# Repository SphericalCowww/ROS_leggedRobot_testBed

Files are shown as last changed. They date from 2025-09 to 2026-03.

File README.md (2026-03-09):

# Testing for Legged Robot using ROS2

Goal: quadruped robot dog with 12 DOF up to a simple walk gait.

Derivation from the following <a href="https://github.com/SphericalCowww/ROS_init_practice">GitHub Repository</a>.

The CAD drawings are "hidden" under this  <a href="https://github.com/SphericalCowww/ROS_leggedRobot_testBed/tree/main/src/my_robot_description/mesh/CADv0.1">path</a> for ROS reason.

## Hardware Connections

| device | DYNAMIXEL models | number | specification |
| - | - | - | - |
| controller | <a href="https://www.raspberrypi.com/products/raspberry-pi-5/">rasp pi 5</a> | 1 | 16Gb RAM | 
| DC-DC step-down convertor | Hailege <a href="https://www.amazon.de/Hailege-Module-Step-Down-Supply-Converter/dp/B07XFMMY1F">24V/12V to 5V/5A</a> | 1 | USB Port port to rasp pi 5,  DC 5.5mm x 2.5mm Male to battery | 
| USB communication interface | DYNAMIXEL <a href="https://emanual.robotis.com/docs/en/parts/interface/u2d2/">U2D2</a> | 1 | Can control 12 servo in daisy chain if properly powered |
| communication/power hub | DYNAMIXEL <a href="https://emanual.robotis.com/docs/en/parts/interface/u2d2_power_hub/">U2D2 power hub board</a> | 2 | Operating voltage	3.5-24V withg a maximum current	of 10A |
| servo motor | DYNAMIXEL <a href="https://emanual.robotis.com/docs/en/dxl/x/xl430-w250/">XL430-W250-T</a> | 12 | Max stall torque: 1.5 N*m (at 12.0V, 1.4A, 1.071 Nm/A) |
| battery | ZYGY <a href="https://www.amazon.de/dp/B0BB6RMM5Q">11.1V 2000mAh</a> | 2 | already includes protection. Need adapters for: T-plug => XT60 Male => DC 5.5mm x 2.5mm Male | 
| bearings | standard bearing, threaded rod, rod-end bearing, <a href="https://www.amazon.de/dp/B01M2ZCLKX">spacer</a> | 8, 4, 4, 4 | as long as the dimensions work out together, but the rod length so far is 60mm |
| bolts and nuts | | | DYNAMIXEL provides most < M3 bolts; use lock nuts; also best to have threaded inserts for 3D-printer materials, but designed choices can get around it |
|  |  |  |  | 
| battery | Palogreen <a href="https://www.amazon.de/dp/B0DZ65LMPT">12.6V DC Akku 2800mAh</a> | - | already includes protection. One for powering the rasp pi 5, and several backups | 
| power supply | SMPS | - | 12V/5A to test 1 leg | 
| battery | <a href="https://secure.reichelt.com/de/en/industrial_cell_18650_3_6_v_2600_mah_unprotected_pack_of_2-p261054.html">SON 18650 VTC5A</a> | - | Operating voltage 3.6-3.7V with a discharge max of 10A each; need 3 parallel of 3 in series | 
| battery management system | <a href="https://powercells.de/3s-40a-12-6v-cell-li-on-akku-batterie-schutz-platine-bms-pcb-lithium-protection.html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">3S 40A 12.6V BSM PCB</a> | - | plan to use one for each of the 3-series battery pack | 
| controller | <a href="https://emanual.robotis.com/docs/en/parts/controller/opencr10/">OpenCR 1.0</a> | - | This is not necessary if a Rasp Pi is already in use |

#### XL430-W250-T dimensions

  * general dimension: 28.5 x 46.5 x 34 [WxHxD mm]
  * screw size: M2 on rotor plate, M2.5 screws on frame corners, M2.6 on frame surfaces
  * <a href="https://en.robotis.com/service/downloadpage.php?ca_id=70">CAD download</a>
  * bracket reference: <a href="https://grabcad.com/library/openmanipulator-x-frame-set-rm-x52-1">OpenManipulator-X</a>

#### 3D CAD dimensions

  * using 3M screws overall, as they are much more common. Piece thickness will be 4mm, except when a 3M screw is required on the thickness axis, then it's 6mm. For aperture dimension, 1.7mm radius for clearance, and 1.25mm for tapped without a heated insert.

### Power System

  * The daisy chain is recommended to chain 4 or fewer servos to avoid delay
  * Plan to use 2 U2D2 power hub boards controlled by one U2D2. Each hub can be powered independently and controlled by a single U2D2 as long as they share the TTL connection. This requires a Y-cable from U2D2 to the 2 hubs; may need to custom-connect two <a href="https://emanual.robotis.com/docs/en/dxl/x/xl320/#connector-information">MOLEX 51065-0300</a> cables to make a Y-cable.
  * Plan to power the hubs using their SMPS DC jacks. Then use the molex/screw terminal as an output to power the Raspberry Pi 5 via a 12V-to-5V DC-DC converter.

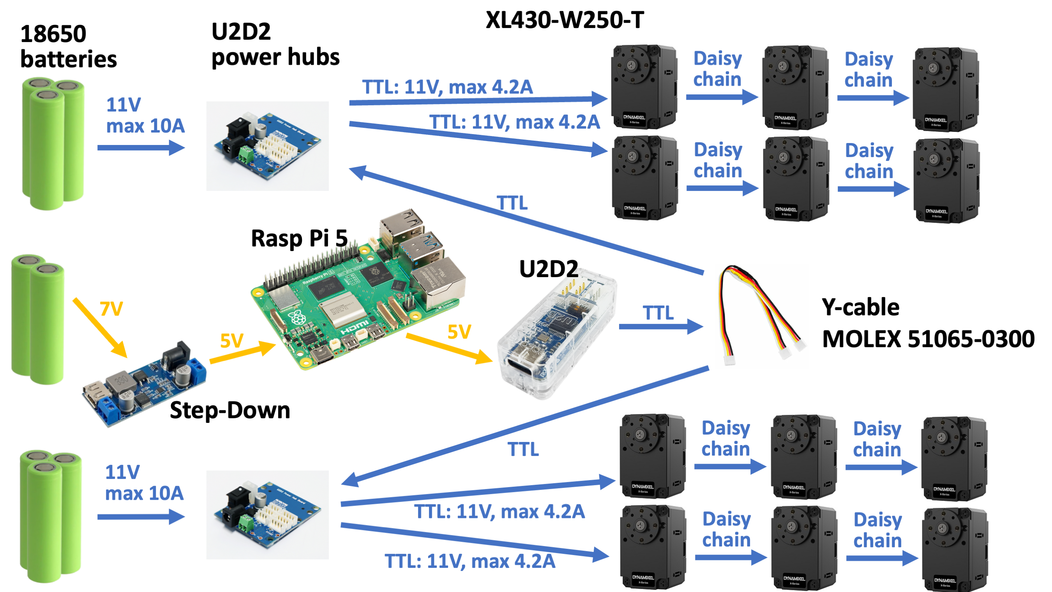
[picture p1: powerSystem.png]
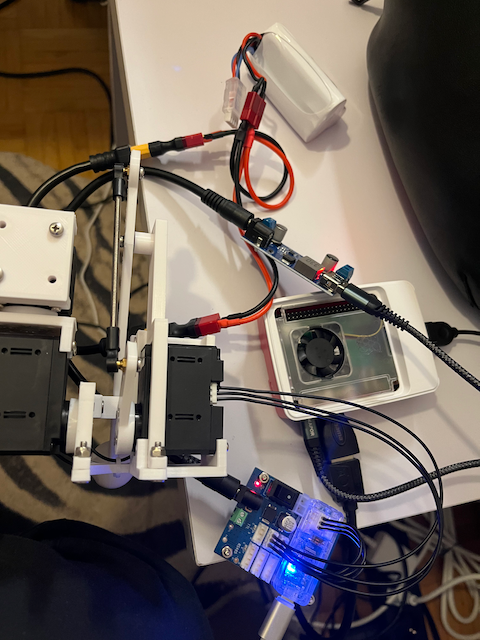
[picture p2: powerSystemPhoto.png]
 

When testing, the 11.1V battery can be teed to power both rasp pi and 3 servos. However, rasp pi does show low power when also turning on the monitor with HDMI connection.

### setting the servo IDs

Connecting servo to U2D2 according to <a href="https://www.youtube.com/watch?v=FIj_NULYOKQ">YouTube</a>:

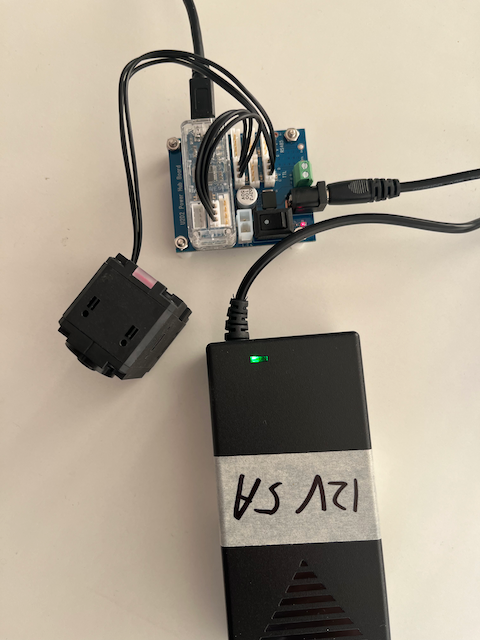
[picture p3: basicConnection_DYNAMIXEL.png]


Use the following App <a href="https://emanual.robotis.com/docs/en/software/dynamixel/dynamixel_wizard2/">DYNAMIXEL Wizard 2.0</a> to change the servo ID (default 1) to, say, ID 10. Note that if any of the servos have the same ID, they will NOT show up in the scan. The servos also all initially come with an ID of 1, so they must be connected one by one to U2D2 to change their IDs accordingly.

    connect U2D2 to computer => open DYNAMIXEL Wizard 2.0
    # Options 
    ## Select protocol to scan => Protocol 2.0 (only)
    ## Select port to scan => which ever port is connected
    ## Select baudrate to scan => 57600 bps and 2000000bpt => OK
    ## Select ID range to scan => End => 50
    ## OK
    # Scan
    # Item 
    ## (Address 7) ID => ID 11 (on the right) => Save (may need to scroll down) 
    ## (Address 8) Baud Rate (Bus) => 2Mbps (on the right) => Save (may need to scroll down) 
    ## (Address 9) Return Delay Time => 0 (on the right) => Save (may need to scroll down) 
    ## (Address 68) Status Return Level => 2 (on the right) => Save (may need to scroll down) 

Can also test out the servo:

    # LED (top right toggle)
    # Torque (top right toggle) => set the value for motion (can select Velocity/Position mode)

### Quadruped: CAD Model and Physical Assembly

One leg assembly needs 3 servos to ensure all 3 degrees of freedom for each of the 4 leg tips:

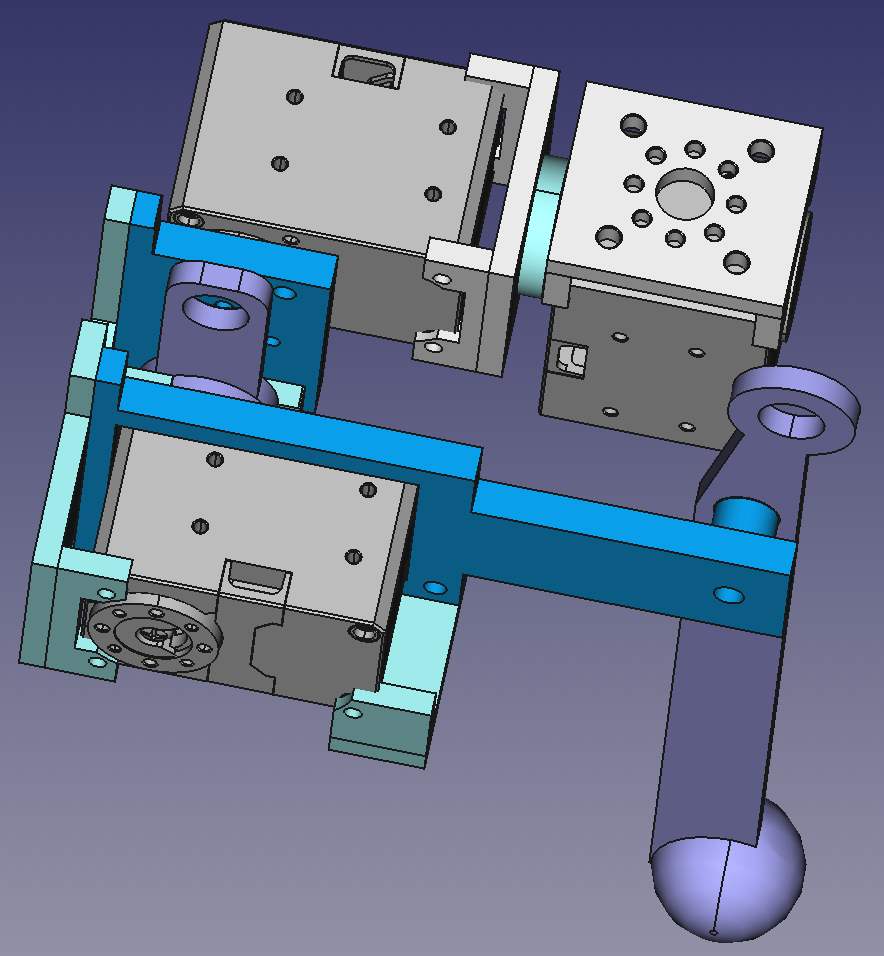
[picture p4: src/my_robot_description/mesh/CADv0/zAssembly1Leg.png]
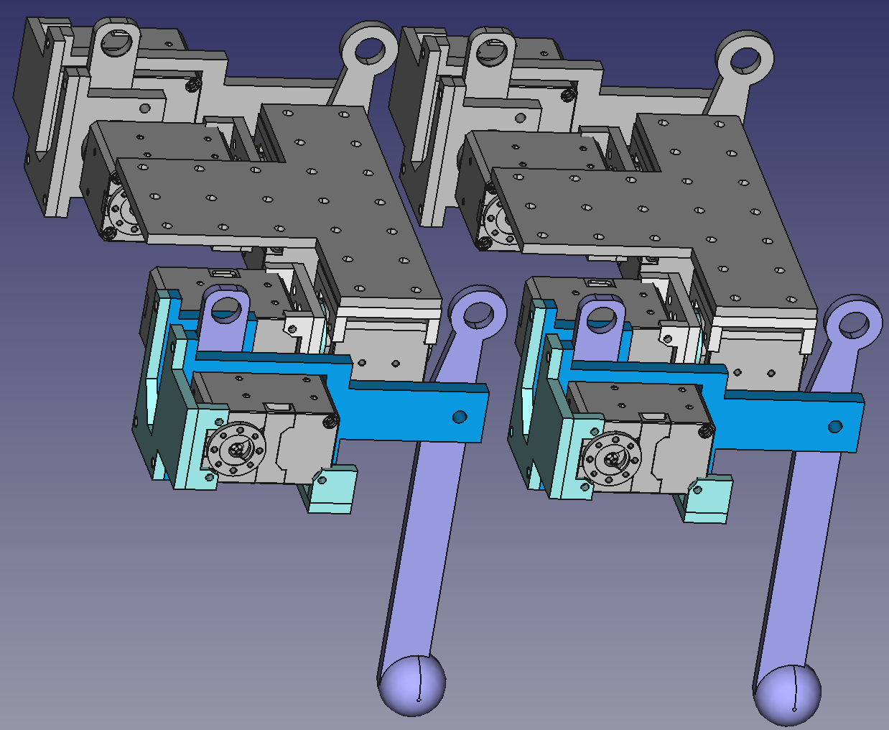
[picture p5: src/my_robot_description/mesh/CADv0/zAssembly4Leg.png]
 

The current design has many flaws, but here is the first assembly:

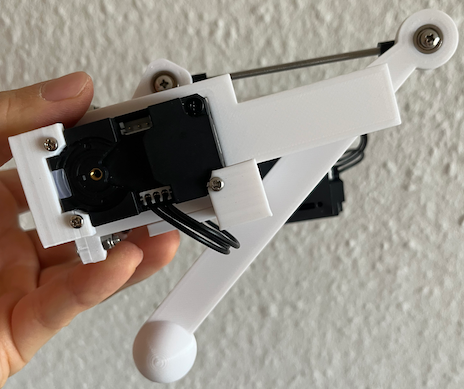
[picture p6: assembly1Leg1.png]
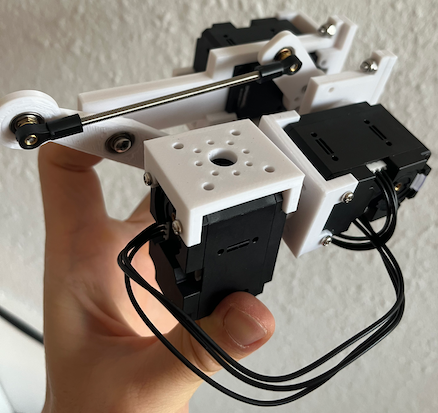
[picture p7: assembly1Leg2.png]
 

[Video demo1](https://raw.githubusercontent.com/SphericalCowww/ROS_leggedRobot_testBed/main/assembly1Leg1.mp4), [video demo2](https://raw.githubusercontent.com/SphericalCowww/ROS_leggedRobot_testBed/main/assembly1Leg2.mp4)

Here is the assembly with the hardware control system: rasp pi 5, DC-DC step-down convertor, U2D2, battery pack, and the existing 1 leg. DO NOT wrap the USB signal cable with the power cables; it would create interference.

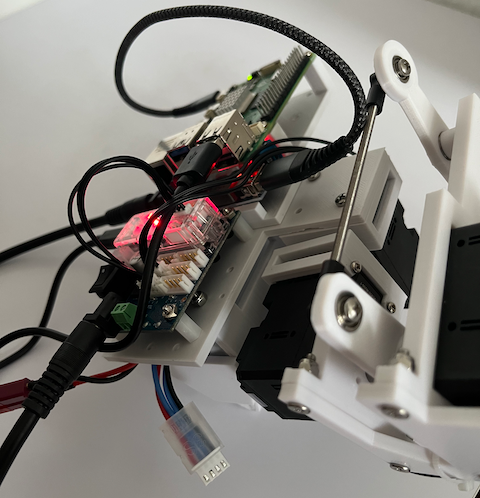
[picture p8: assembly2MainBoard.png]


Here is the full assembly. Also updated the unnecessary bearing at the connection of the universal bearings. The robot has a total weight of roughly 2kg.

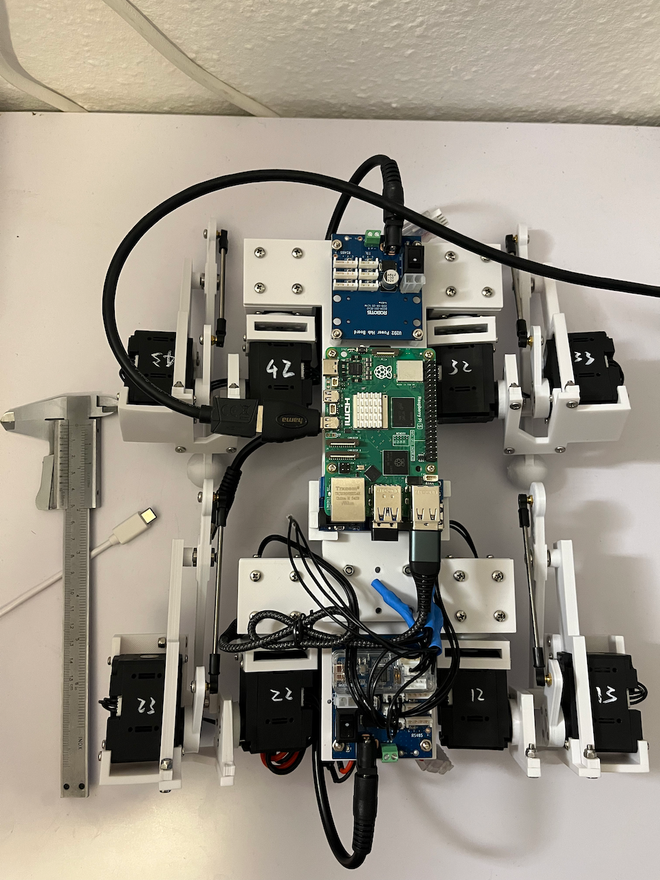
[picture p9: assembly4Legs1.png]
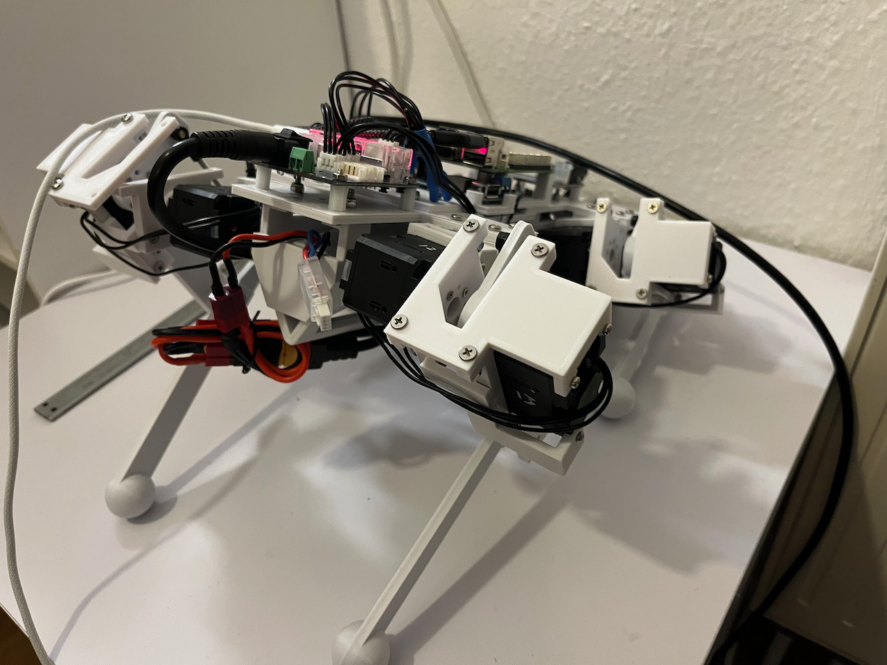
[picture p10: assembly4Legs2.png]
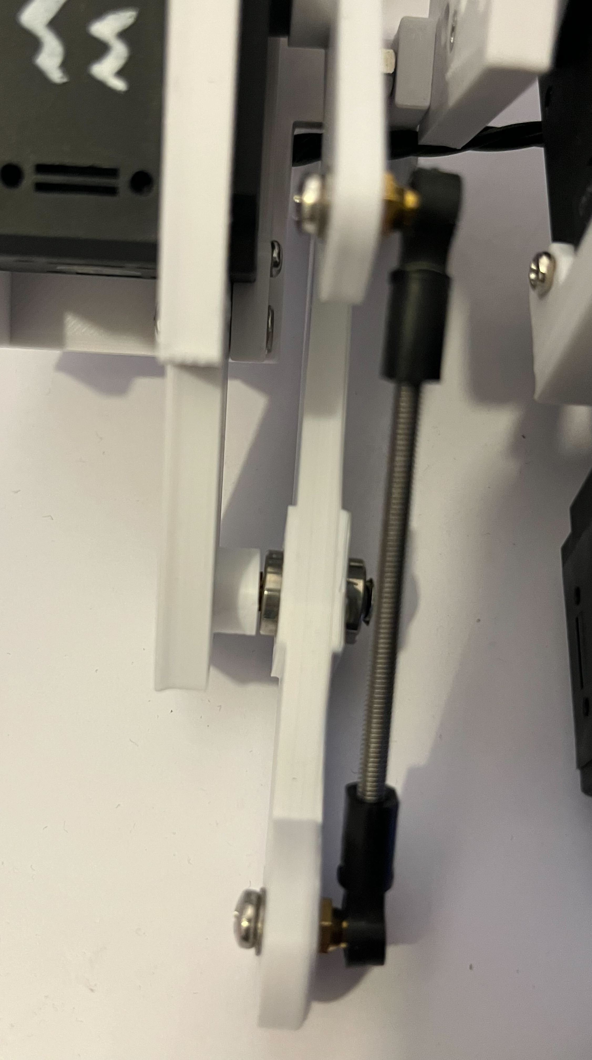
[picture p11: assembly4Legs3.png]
  

## Installing the <a href="https://github.com/ROBOTIS-GIT/DynamixelSDK">dynamixel-sdk</a> and  <a href="https://github.com/ROBOTIS-GIT/dynamixel-workbench">dynamixel-workbench</a>

Following <a href="https://github.com/SphericalCowww/ROS_init_practice">github</a> to install ROS. To install drivers for Dynamixel, 

    sudo apt install ros-jazzy-dynamixel-sdk* ros-jazzy-dynamixel-hardware* ros-jazzy-dynamixel-workbench*
    dpkg -l | grep dynamixel
    ros2 pkg list | grep dynamixel

Then copy <a href="https://github.com/ROBOTIS-GIT/dynamixel-workbench/tree/main/dynamixel_workbench_toolbox/examples/src">src</a> directly under ``/src/my_toolbox_dynamixel_workbench``. And for every ``.cpp`` file, change the following line:

    #include <DynamixelWorkbench.h>

To, 

    #include <cstdlib>
    #include "dynamixel_workbench_toolbox/dynamixel_workbench.h"

Then ``cd ROS_leggedRobot_testBed`` and build,

    colcon build
    source install/setup.bash

Connect U2D2 to Rasp Pi USB port: 

    sudo dmesg | tail -n 20
    # look for:
    ## usb 2-2: Detected FT232H
    ## usb 2-2: FTDI USB Serial Device converter now attached to ttyUSB0
    ls -l /dev/ttyUSB*
    sudo chmod a+rw /dev/ttyUSB0                   # required everytime after reconnection
    ros2 run my_toolbox_dynamixel_workbench model_scan /dev/ttyUSB0 57600
    ros2 run my_toolbox_dynamixel_workbench position /dev/ttyUSB0 57600 11 0.5

Update USB port latency to 1 ms. Note that this USB signal is delicate, use as short and as high quality of the USB cable as possible.: 

    lsusb
    # look for: Bus 002 Device 003: ID 0403:6014 Future Technology Devices International, Ltd FT232H Single HS USB-UART/FIFO IC
    sudo vim /etc/udev/rules.d/99-dynamixel-latency.rules
    ---------- add: 
    SUBSYSTEM=="tty", ATTRS{idVendor}=="0403", ATTRS{idProduct}=="6014", ATTR{device/latency_timer}="1", SYMLINK+="ttyU2D2", MODE="0666", GROUP="dialout"
    # ATTR{device/latency_timer}="1": Sets the 1ms latency (The "Sync Read" fix).
    # SYMLINK+="ttyU2D2": (Optional but helpful) This creates a static name for your device. You can now use /dev/ttyU2D2 in your code instead of /dev/ttyUSB0, so it won't break if you plug in another USB device.
    # MODE="0666": Allows your ROS node to access the port without needing sudo.
    ---------- 
    sudo vim /etc/udev/rules.d/99-ftdi.rules
    ---------- add: 
    SUBSYSTEM=="usb", ATTR{idVendor}=="0403", ATTR{idProduct}==6014, MODE="0666", GROUP="dialout"
    SUBSYSTEM=="tty", ATTRS{idVendor}=="0403", ATTRS{idProduct}=="6014", MODE="0666", GROUP="dialout"
    # This gives the correct permission to the USB port in question, otherwise, whenever reconnected, needs to do: sudo chmod a+rw /dev/ttyUSB0
    ---------- 
    sudo udevadm control --reload-rules
    sudo udevadm trigger
    ls -l /dev/ttyU2D2
    # if doesn't exist, do: sudo apt remove brltty
    cat /sys/class/tty/ttyUSB0/device/latency_timer
    # which should show 1 for 1 ms

Update to run the firmware with proper permissions to avoid latency:

    # without sudo, we will see the following WARNING in ros2 launch:
    ## [ros2_control_node-2] [WARN] [1766867979.090889912] [controller_manager]: Could not enable FIFO RT scheduling policy: with error number <1> (Operation not permitted). See [https://control.ros.org/master/doc/ros2_control/controller_manager/doc/userdoc.html] for details on how to enable realtime scheduling.
    # with sudo, we can do the following:
    ## sudo bash -c "source /opt/ros/jazzy/setup.bash; source install/setup.bash; ros2 launch my_robot_bringup my_robot.with_commander.launch.py"
    # however, eventually we want to run without sudo in case it messes up with other permissions:
    sudo addgroup realtime
    sudo usermod -a -G realtime $USER
    sudo vim /etc/security/limits.d/realtime.conf:
    ----------  add:
    @realtime soft rtprio 99
    @realtime soft priority 99
    @realtime soft memlock unlimited
    @realtime hard rtprio 99
    @realtime hard priority 99
    @realtime hard memlock unlimited
    ---------- 
    sudo reboot
    # 

## Testing ROS2 interface with a simulated robot arm

### testing the driver in ROS2

    colcon build
    source install/setup.bash
    ros2 run my_robot_firmware testRaspPi5_dynamixel_u2d2_leg1swing_xl430
    ps -ef | grep testRaspPi5_dynamixel_u2d2_leg1swing_xl430                 # to kill it before it ends
    # only when dynamixels are not connected to into a leg: 
    ## ros2 run my_robot_firmware testRaspPi5_dynamixel_u2d2_channel0_xl430 
    ## ros2 run my_robot_firmware testRaspPi5_dynamixel_u2d2_leg1swipe_xl430

### testing MoveIt with Gazebo

    colcon build
    source install/setup.bash
    ros2 launch my_robot_bringup ma_robot.gazebo.launch.with_commander.py
    ros2 topic pub -1 /arm_set_pose my_robot_interface/msg/MaRobotArmPoseTarget "{x: 0.7, y: 0.0, z: 0.4, roll: 3.14, pitch: 0.0, yaw: 0.0, use_cartesian_path: false}"

### testing the driver with ros2_control and MoveIt
Under ``ma_robot.ros2_control.xacro``, switch ``<plugin>mock_components/GenericSystem</plugin-->`` to ``<plugin>ma_robot_namespace::HardwareInterfaceU2D2_ma_robot</plugin>``. The latter plugin type can be found at the bottom of ``src/my_robot_firmware/hardware_interface_ma_robot_dynamixel_u2d2_xl430.xml``. Then run the following:

    colcon build
    source install/setup.bash
    ros2 launch my_robot_bringup ma_robot.with_commander.launch.py
    ros2 topic info /arm_set_name
    ros2 topic pub -1 /arm_set_named example_interfaces/msg/String "{data: "arm_pose1"}"
    ros2 topic info /arm_set_joint
    ros2 topic pub -1 /arm_set_joint example_interfaces/msg/Float64MultiArray "{data: [0.5, 0.5, 0.5, 0.5, 0.5, 0.5]}"
    ros2 topic info /arm_set_pose
    ros2 topic pub -1 /arm_set_pose my_robot_interface/msg/MaRobotArmPoseTarget "{x: 0.7, y: 0.0, z: 0.4, roll: 3.14, pitch: 0.0, yaw: 0.0, use_cartesian_path: false}"
    ros2 topic info /gripper_set_open
    ros2 topic pub -1 /gripper_set_open example_interfaces/msg/Bool "{data: false}"

## Launch ROS2 interface with 1 leg

### launch urdf

Then run the following:

    colcon build
    source install/setup.bash
    ros2 launch my_robot_description my_robot.rviz.launch.xacro.py
    # if no config loaded
    ## Fixed Frame: base_link
    ## Add: RobotModel
    ## RobotModel: Description Topic: /robot_description

[Video demo](https://raw.githubusercontent.com/SphericalCowww/ROS_leggedRobot_testBed/main/rViz1Leg.mp4)

### moveit2 setup assistance with a leg

Launch the MoveIt assistance:

    sudo apt update
    sudo apt install
    colcon build
    source install/setup.bash
    ros2 launch moveit_setup_assistant setup_assistant.launch.py
    # Create New Moveit Configuration Package (or edit if the configuration files already exist)
    # Browse => src/my_robot_description/urdf/my_robot.urdf.xacro => Load Files
    # Start Screen: can toggle visual/collision
    # Self-Collisions => Generate Collision Matrix: removes all never-in-contact and adjacent collisions
    # Virtual Joints => Add Virtual Joint => Virtual Joint Name: virtual_joint => Parent Frame Name: world => Joint Type: fixed => Save
    ## no need if already defined in urdf. Can always comment out afterwards in /src/my_robot_moveit_config/config/my_robot.srdf 
    # Planning Groups => Add Group => Group Name: leg1 => Kinametic Solver: kdl_kinematics_plugin => Add Joints => 
    ## choose with right arrow "servo1_servo1_padding", "servo2_servo2_padding", "servo3_calfFeet", and "calfFeet_calfSphere" => Save
    # Robot Poses => Add Pose => all joints at 0 => Pose Name: home => Save: can add a few other ones for debugging
    # ros2_control URDF Model => position for Command Interfaces and State Interfaces => Add interfaces
    # ROS2 Controllers => Auto Add JointTrajectoryController
    # Moveit Controllers => Auto Add FollowJointsTrajectory
    # Author Information => add anything (e.g. "my_robot", "my_robot@gmail.com"), otherwise bugged
    # Configuration Files => Browse: src/my_robot_moveit_config/ => Generate Package: double check if files are generated => Exit Setup Assistant

Fix the following file:

    # src/my_robot_moveit_config/config/joint_limits.yaml => max_velocity: 20.0, has_acceleration_limits: true, max_acceleration: 10.0 (need to be float)
    # src/my_robot_moveit_config/config/moveit_controllers.yaml => add the following under leg1_controller: 
    ## action_ns: follow_joint_trajectory
    ## default: true
    # src/my_robot_moveit_config/config/initial_positions.yaml => servo1_servo1_padding: 3.14, servo2_servo2_padding: 3.14, servo3_calfJoint: 3.14
    # src/my_robot_moveit_config/config/my_robot.srdf => include only the following in <group name="leg1">:
    ## <group name="leg1">
    ##     <chain base_link="base_link" tip_link="calfSphere"/>
    ## </group>
    # src/my_robot_moveit_config/config/kinematics.yaml => replace with the following:
    ##leg1:
    ##  kinematics_solver: kdl_kinematics_plugin/KDLKinematicsPlugin
    ##  kinematics_solver_search_resolution: 0.005
    ##  kinematics_solver_timeout: 0.05
    ##  kinematics_solver_attempts: 3
    ##  position_only_ik: True        # this one is important because the leg does NOT care about the orientation of the end effector

### launch the demo:

    colcon build
    source install/setup.bash
    ros2 launch my_robot_moveit_config demo.launch.py
    # ignore: [move_group-3] [ERROR] [1758361830.007872451] [move_group.moveit.moveit.ros.occupancy_map_monitor]: No 3D sensor plugin(s) defined for octomap updates
    # ignore: [rviz2-4] [ERROR] [1758361834.128908606] [moveit_143394722.moveit.ros.motion_planning_frame]: Action server: /recognize_objects not available
    # MotionPlanning:
    ## Planning Group: leg1
    ## Goal State: pose1
    ## Plan
    ## Execute

Note that to move the motion wheel in rViz:

    # toggle: Approx IK Soluations
    # toggle if needed: MotionPlanning => Planned Path => Loop Animation
    # toggle if needed: Use Cartesian Path 

### launch with a proper launch file:

    mv src/my_robot_moveit_config/config/ros2_controllers.yaml src/my_robot_bringup/config/my_robot_controllers.yaml
    # change the following line if needed in my_robot_controllers.yaml
    ## update_rate: 100 # Hz
    mv src/my_robot_moveit_config/config/my_robot.ros2_control.xacro src/my_robot_description/urdf/
    rm src/my_robot_moveit_config/config/my_robot.urdf.xacro
    # modify the following line in my_robot.ros2_control.xacro:
    ## remove: <xacro:property name="initial_positions" value="${xacro.load_yaml(initial_positions_file)['initial_positions']}"/>
    ## for all servos, update to: <param name="initial_value">3.14</param> 
    # adding the following line in my_robot.urdf.xacro:
    ## <xacro:include filename="my_robot.ros2_control.xacro" />
    colcon build
    source install/setup.bash
    ros2 launch my_robot_bringup my_robot.launch.py
    # NOTE: Sometimes it takes a second try to have everything registered
    # Add => MotionPlanning
    ## Context => Planning Library => ompl
    ## Planning => Goal State: pose1 => Plan => Execute

### launch with gazebo, command line enabled

    colcon build
    source install/setup.bash
    ros2 launch my_robot_bringup my_robot.gazebo.with_commander.launch.py
    ros2 topic pub -1 /leg1_set_named example_interfaces/msg/String "{data: "pose1"}"

### launch with hardware, command line enabled
Under ``my_robot.ros2_control.xacro``, switch ``<plugin>mock_components/GenericSystem</plugin-->`` to ``<plugin>my_robot_namespace::HardwareInterfaceU2D2_my_robot</plugin>``. 

  * src/my_robot_**bringup**/launch/**my_robot.with_commander.launch.py**
    * src/my_robot_description/urdf/my_robot.urdf.xacro
      * src/my_robot_description/urdf/common_properties.xacro
      * src/my_robot_description/urdf/my_robot_arm.xacro.xacro
      * src/my_robot_description/urdf/my_robot_gripper.xacro.xacro
      * src/my_robot_**description**/urdf/**my_robot.ros2_control.xacro**
        * src/my_robot_firmware/hardware_interface_my_robot_dynamixel_u2d2_xl430.xml
        * src/my_robot_**firmware**/include/my_robot_firmware/**hardware_interface_my_robot_dynamixel_u2d2_xl430.hpp**
    * src/my_robot_**bringup**/config/**my_robot_controllers.yaml**
      * joint_trajectory_controller/JointTrajectoryController
    * src/**my_robot_moveit_config**/launch/**move_group.launch.py**
      * src/my_robot_moveit_config/config...
    * src/my_robot_commander/src/**my_robot_commander.cpp**
      * src/my_robot_interface/msg/MyRobotLeg1PoseTarget.msg
    * src/my_robot_description/rviz/my_robot.urdf_config.rviz

Then run the following:

    colcon build
    source install/setup.bash
    ros2 launch my_robot_bringup my_robot.with_commander.launch.py
    # on another window
    ros2 topic pub -1 /leg1_set_named example_interfaces/msg/String "{data: "pose1"}"
    ros2 topic pub -1 /leg1_set_joint example_interfaces/msg/Float64MultiArray "{data: [3.14, 3.14, 3.14]}"
    ros2 topic pub -1 /leg1_set_pose my_robot_interface/msg/MyRobotLeg1PoseTarget "{x: -0.092, y: 0.053, z: 0.135, use_cartesian_path: false}" 
    ros2 topic pub -1 /leg1_set_walk example_interfaces/msg/String "{data: "walk1"}" # demo in the .mp4

[Video demo1](https://raw.githubusercontent.com/SphericalCowww/ROS_leggedRobot_testBed/main/walkGait0_1Leg.mp4)
    
    # for debugging
    ros2 topic echo /joint_states # use this to track servo positions instead of printing out in src/my_robot_firmware/hardware_interface_my_robot_dynamixel_u2d2_xl430.xml
    ros2 topic hz /joint_states
    ros2 run tf2_tools view_frames
    ros2 param list /move_group | grep kinematics
    ros2 param get /move_group robot_description_kinematics.leg1.kinematics_solver

Note the Cartesian path currently does work due to <a href="https://github.com/moveit/moveit2/issues/3658">moveit issue</a>. For debugging:

    ros2 param get /move_group jump_threshold
    ros2 param list /move_group

#### PILZ planning

Industrial robot arm planning (see <a href="https://moveit.picknik.ai/main/doc/how_to_guides/pilz_industrial_motion_planner/pilz_industrial_motion_planner.html">reference</a>), which is likely too stringent and slow for walk-gait:

    colcon build
    source install/setup.bash
    ros2 launch my_robot_bringup my_robot.with_commander.launch.py
    # on another window, first move to the starting position
    ros2 topic pub -1 /leg1_set_pose my_robot_interface/msg/MyRobotLeg1PoseTarget "{x: -0.09, y: 0.01, z: 0.13, use_cartesian_path: false}" 
    ros2 topic pub -1 /leg1_set_walk example_interfaces/msg/String "{data: "walk5"}"

Also, use the following to track the rasp pi cpu temperature in case the planning is overclocking the CPU:

    sudo vcgencmd measure_temp

[Video demo1](https://raw.githubusercontent.com/SphericalCowww/ROS_leggedRobot_testBed/main/walkGait1_1Leg.mp4)

#### IPTP/TOTG planning

The usual moveit execution always stops at each pose before starting another. The Iterative Parabolic Time Parameterization (IPTP) or Time Optimal Trajectory Generation (TOTG) on a manually constructed joint trajectory should smooth out the walk-gait. The IK can be taken out of the while loop too, reducing the processing time of repeated motion.

    colcon build
    source install/setup.bash
    ros2 launch my_robot_bringup my_robot.with_commander.launch.py
    # on another window, first move to the starting position
    ros2 topic pub -1 /leg1_set_walk example_interfaces/msg/String "{data: "walk6"}"

Note, turns out IPTP is not supported by the newest moveit2 by default.

[Video demo2](https://raw.githubusercontent.com/SphericalCowww/ROS_leggedRobot_testBed/main/walkGait2_1Leg.mp4)

### launch with hardware, commander as a lifecycle

    ros2 launch my_robot_bringup my_robot.with_lifecycle.launch.py
    ros2 lifecycle set /my_robot_lifecycle configure
    ros2 lifecycle set /my_robot_lifecycle activate
    ros2 service call /get_robot_state std_srvs/srv/Trigger {}            # to get the current position
    ros2 topic pub -1 /leg1_set_named example_interfaces/msg/String "{data: "pose1"}"
    ros2 topic pub -1 /leg1_set_joint example_interfaces/msg/Float64MultiArray "{data: [3.14, 3.14, 3.14]}"
    ros2 topic pub -1 /leg1_set_pose my_robot_interface/msg/MyRobotLeg1PoseTarget "{x: -0.09, y: 0.01, z: 0.13, use_cartesian_path: false}" 
    ros2 service call /leg1_walk_toggle std_srvs/srv/SetBool "{data: true}"

## Launch Cubic Doggo with 4 legs

### launch with hardware, commander as a lifecycle

    ros2 launch my_robot_bringup cubic_doggo.with_lifecycle.launch.py
    ros2 topic pub -1 /leg_set_named example_interfaces/msg/String "{data: "rest"}"
    ros2 topic pub -1 /leg_set_named example_interfaces/msg/String "{data: "stand"}"
    ros2 topic pub -1 /leg_set_named example_interfaces/msg/String "{data: "sit"}"
    ros2 topic pub -1 /leg_set_joint example_interfaces/msg/Float64MultiArray "{data: [0, 3.14, 3.14, 3.54]}"
    ros2 topic pub -1 /leg_set_pose my_robot_interface/msg/CubicDoggoLegPoseTarget "{leg_index: 0, x: -0.092, y: 0.053, z: 0.135}" 
    ros2 service call /leg_walk_toggle std_srvs/srv/SetBool "{data: true}"

Here is the standing post:

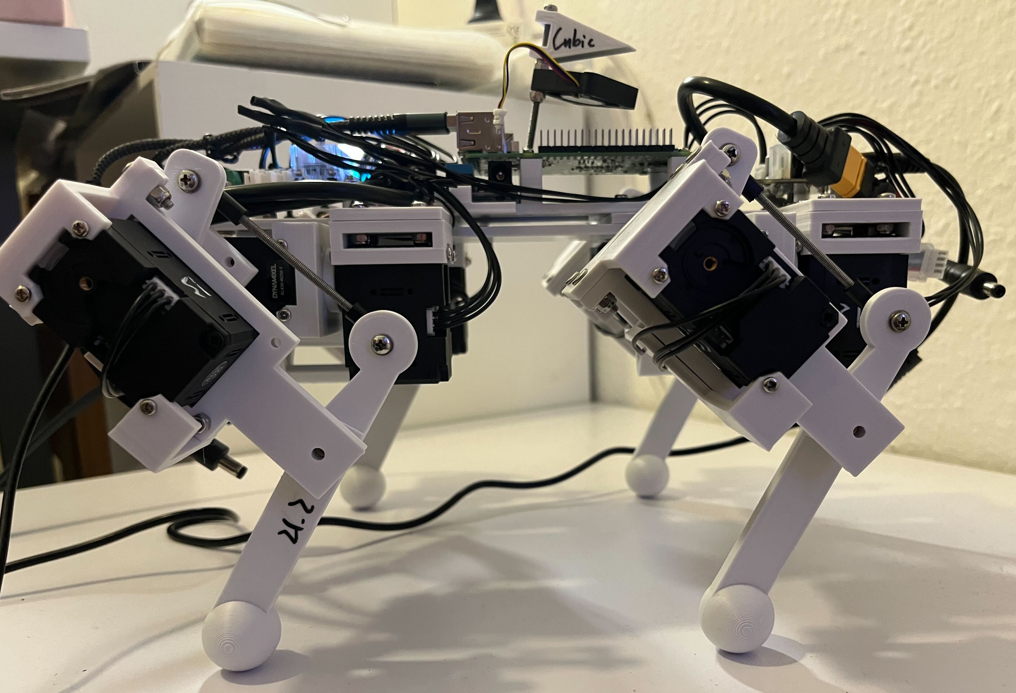
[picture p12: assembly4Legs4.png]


Here is the standing action. It turns out that with proper leg proportions, the motors are very capable of doing this (consult LLM for proper leg dimensions given the weight and torque):

[Video demo](https://raw.githubusercontent.com/SphericalCowww/ROS_leggedRobot_testBed/main/standAction0_4Leg.mp4)

Here is the simplest walk gait one can implement:

[Video demo](https://raw.githubusercontent.com/SphericalCowww/ROS_leggedRobot_testBed/main/walkGait0_4Leg.mp4)

### launch at the start of turning on rasp pi

    chmod +x /home/kali/Documents/ROS_leggedRobot_testBed/start_robot.sh
    sudo vim /etc/systemd/system/robot_startup.service
    # filling the following:
    ## [Unit]
    ## Description=Cubic Doggo Robot Bringup
    ## After=network.target
    ## [Service]
    ## Type=simple
    ## User=cubicdoggo
    ## ExecStart=/home/cubicdoggo/Documents/ROS_leggedRobot_testBed/start_robot.sh
    ## Restart=on-failure
    ## RestartSec=5
    ## [Install]
    ## WantedBy=multi-user.target
    sudo systemctl daemon-reload                      # reload whenever there is a change
    sudo systemctl enable robot_startup.service       # now will start at reboot
    # sudo systemctl start robot_startup.service        # start right now too
    # sudo systemctl stop robot_startup.service         # stop right now
    # sudo systemctl disable robot_startup.service      # disable at reboot

## References:
- Guiding Video => AstroSam, I Made a Robot Dog (2024) (<a href="https://www.youtube.com/watch?v=XvKlplncafQ">YouTube</a>)

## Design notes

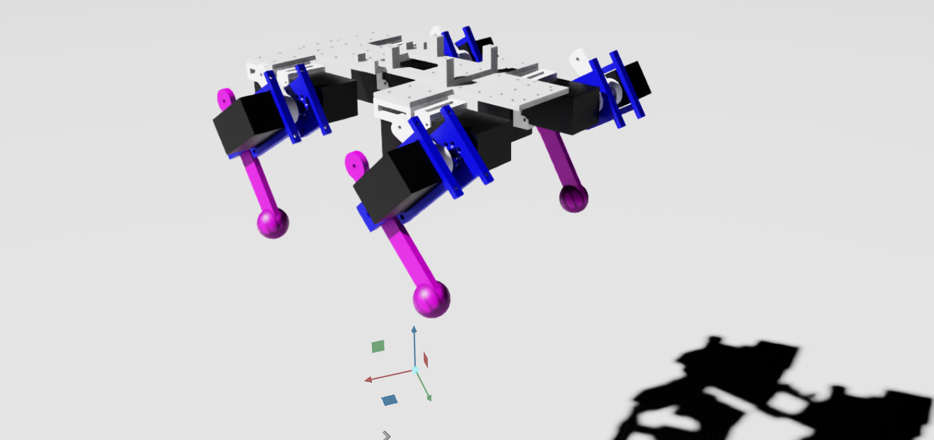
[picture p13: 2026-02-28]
IsaacSimImport.png

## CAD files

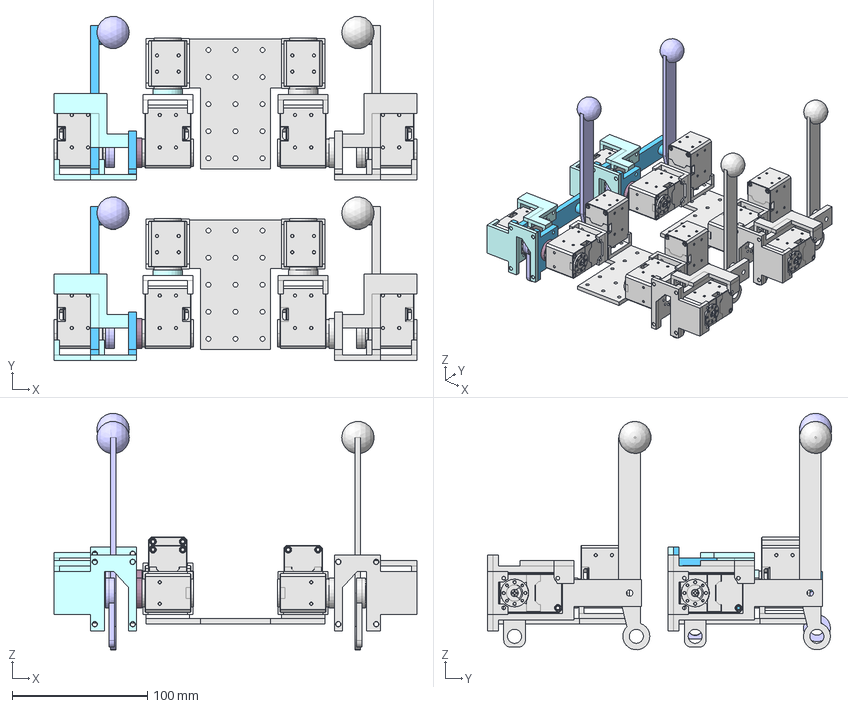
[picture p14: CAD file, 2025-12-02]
src/my_robot_description/mesh/CADv0/zAssembly4Leg.FCStd
268.0 x 254.3 x 174.8 mm
_mod_basePlate1
_mod_XL-430holderBasic_1
DC11_A01_DUMMY
DC12_A01_SPACER_RING
DC12_A01_SPACER_RING001
DC12_A01_SPACER_RING002
DC12_A01_SPACER_RING003
DC12_A01_SPACER_RING004
DC12_A01_SPACER_RING005
DC12_A01_SPACER_RING006
DC12_A01_SPACER_RING007
DC11_A01_IDLER_DUMMY
DC11_A01_IDLER_CAP_DUMMY
_mod_XL-430rotorPadding_1
_mod_XL-430holderBasic_2
DC11_A01_DUMMY001
DC12_A01_SPACER_RING008
DC12_A01_SPACER_RING009
DC12_A01_SPACER_RING010
DC12_A01_SPACER_RING011
DC12_A01_SPACER_RING012
DC12_A01_SPACER_RING013
DC12_A01_SPACER_RING014
DC12_A01_SPACER_RING015
DC11_A01_IDLER_DUMMY001
DC11_A01_IDLER_CAP_DUMMY001
_mod_XL-430rotorPadding_2
_mod_XL-430holderThighFront
DC11_A01_DUMMY002
DC12_A01_SPACER_RING016
DC12_A01_SPACER_RING017
DC12_A01_SPACER_RING018
DC12_A01_SPACER_RING019
DC12_A01_SPACER_RING020
DC12_A01_SPACER_RING021
DC12_A01_SPACER_RING022
DC12_A01_SPACER_RING023
DC11_A01_IDLER_DUMMY002
DC11_A01_IDLER_CAP_DUMMY002
_mod_calfJoint
_mod_thighOuter_heatInsert
calfFeet
_mod_thighInner
_mod_XL-430holderThighBack
zAssembly1Leg11 (Mirror #1)
_mod_basePlate002
zAssembly1Leg11 (Mirror #1)001
_mod_XL-430holderBasic_003
DC11_A01_DUMMY003
DC12_A01_SPACER_RING024
DC12_A01_SPACER_RING025
DC12_A01_SPACER_RING026
DC12_A01_SPACER_RING027
DC12_A01_SPACER_RING028
DC12_A01_SPACER_RING029
DC12_A01_SPACER_RING030
DC12_A01_SPACER_RING031
DC11_A01_IDLER_DUMMY003
DC11_A01_IDLER_CAP_DUMMY003
_mod_XL-430rotorPadding_003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

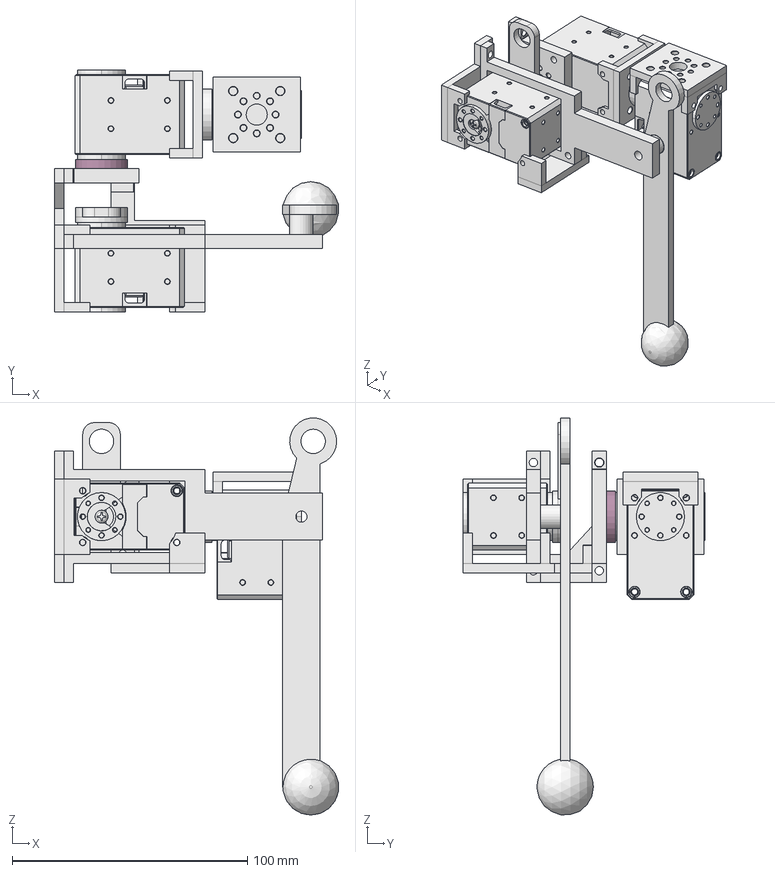
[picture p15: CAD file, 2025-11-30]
src/my_robot_description/mesh/CADv0/zAssembly1Leg.FCStd
120.8 x 103.0 x 168.8 mm
_mod_XL-430holderBasic_1
DC11_A01_DUMMY
DC12_A01_SPACER_RING
DC12_A01_SPACER_RING001
DC12_A01_SPACER_RING002
DC12_A01_SPACER_RING003
DC12_A01_SPACER_RING004
DC12_A01_SPACER_RING005
DC12_A01_SPACER_RING006
DC12_A01_SPACER_RING007
DC11_A01_IDLER_DUMMY
DC11_A01_IDLER_CAP_DUMMY
_mod_XL-430rotorPadding_1
_mod_XL-430holderBasic_2
DC11_A01_DUMMY001
DC12_A01_SPACER_RING008
DC12_A01_SPACER_RING009
DC12_A01_SPACER_RING010
DC12_A01_SPACER_RING011
DC12_A01_SPACER_RING012
DC12_A01_SPACER_RING013
DC12_A01_SPACER_RING014
DC12_A01_SPACER_RING015
DC11_A01_IDLER_DUMMY001
DC11_A01_IDLER_CAP_DUMMY001
_mod_XL-430rotorPadding_2
_mod_XL-430holderThighFront
DC11_A01_DUMMY002
DC12_A01_SPACER_RING016
DC12_A01_SPACER_RING017
DC12_A01_SPACER_RING018
DC12_A01_SPACER_RING019
DC12_A01_SPACER_RING020
DC12_A01_SPACER_RING021
DC12_A01_SPACER_RING022
DC12_A01_SPACER_RING023
DC11_A01_IDLER_DUMMY002
DC11_A01_IDLER_CAP_DUMMY002
_mod_calfJoint
_mod_thighOuter_heatInsert
calfFeet
_mod_thighInner
_mod_XL-430holderThighBack

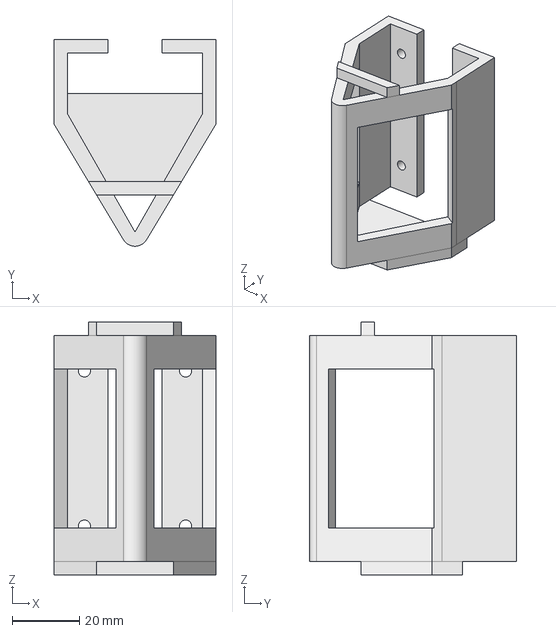
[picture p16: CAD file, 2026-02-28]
src/my_robot_description/mesh/CADv0.1/batteryHolder.FCStd
48.0 x 61.2 x 75.0 mm

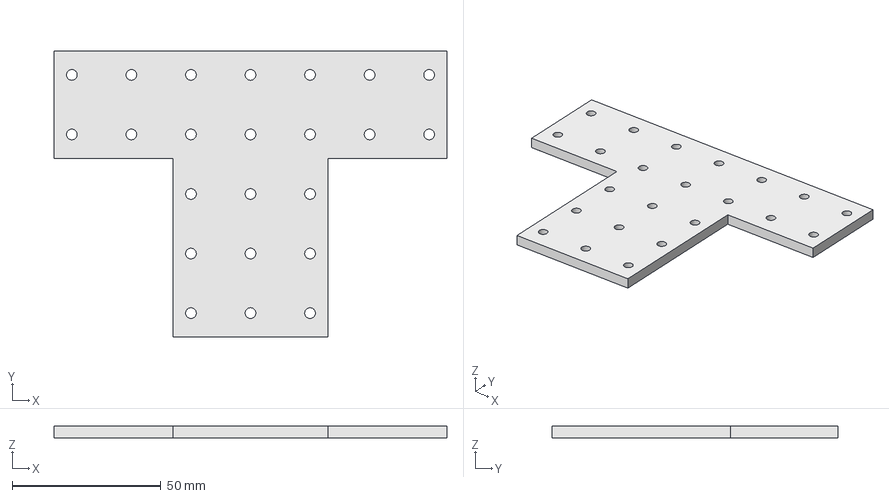
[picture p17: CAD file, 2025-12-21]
src/my_robot_description/mesh/CADv0/_mod_basePlate.FCStd
132.0 x 96.0 x 4.00 mm

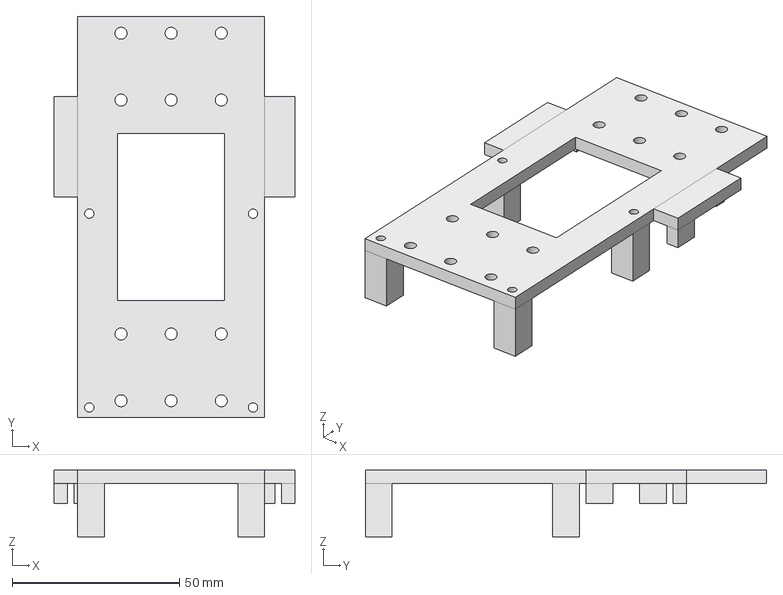
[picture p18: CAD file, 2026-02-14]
src/my_robot_description/mesh/CADv0.1/basePlateTorsoUpper.FCStd
72.0 x 120.0 x 20.0 mm

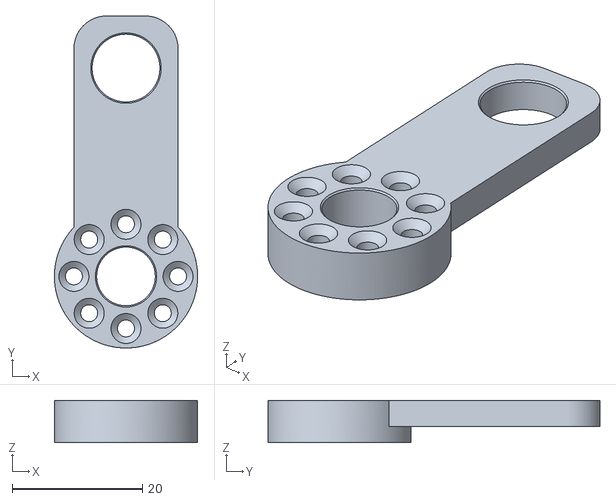
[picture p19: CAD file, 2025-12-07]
src/my_robot_description/mesh/CADv0/_mod_calfJoint-Body.stl
22.0 x 51.0 x 6.50

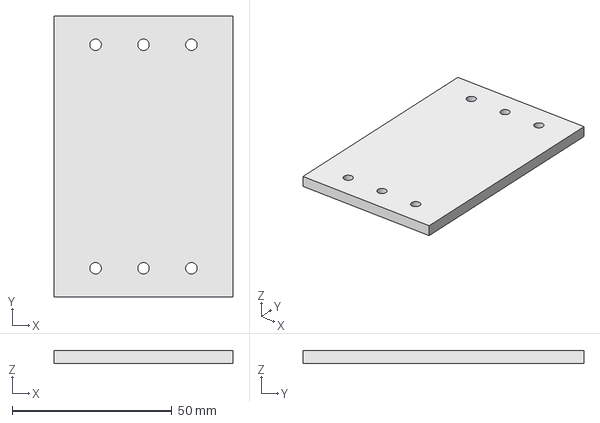
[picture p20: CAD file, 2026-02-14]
src/my_robot_description/mesh/CADv0.1/basePlateTorsoLower.FCStd
56.0 x 88.0 x 4.00 mm

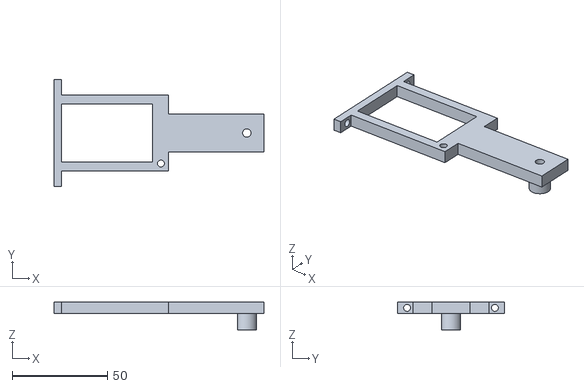
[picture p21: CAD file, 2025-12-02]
src/my_robot_description/mesh/CADv0/_mod_thighOuter_heatInsert-Body.stl
110.0 x 56.0 x 14.5

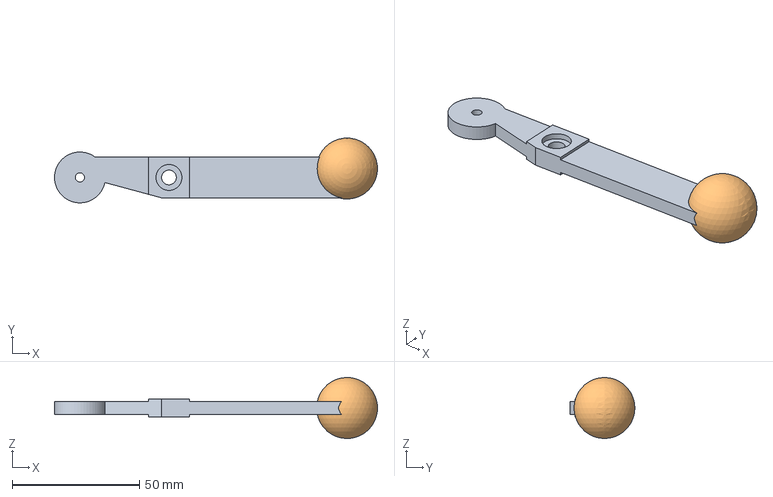
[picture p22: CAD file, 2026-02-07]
src/my_robot_description/mesh/CADv0.1/calfFeet.FCStd
127.0 x 25.5 x 24.0 mm

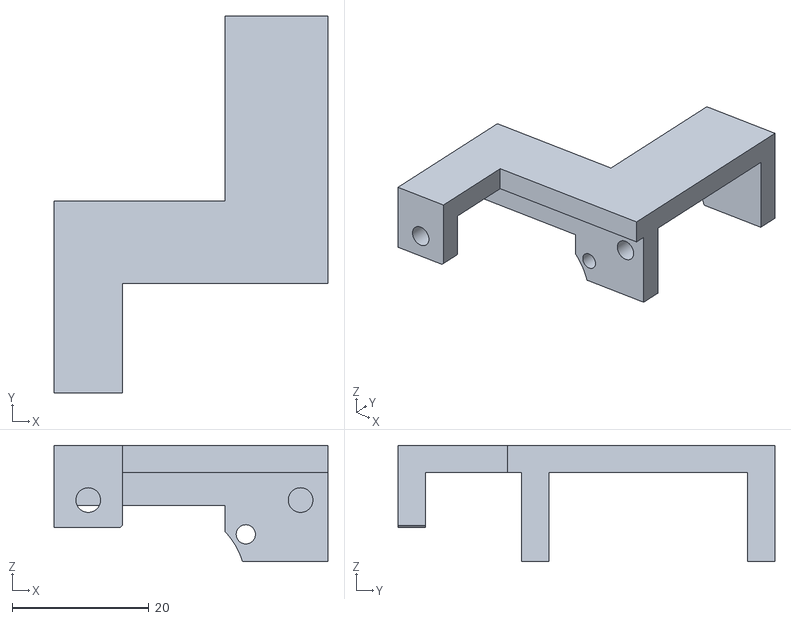
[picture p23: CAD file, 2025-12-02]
src/my_robot_description/mesh/CADv0/_mod_XL-430holderThighBack-Body.stl
40.0 x 55.0 x 17.0

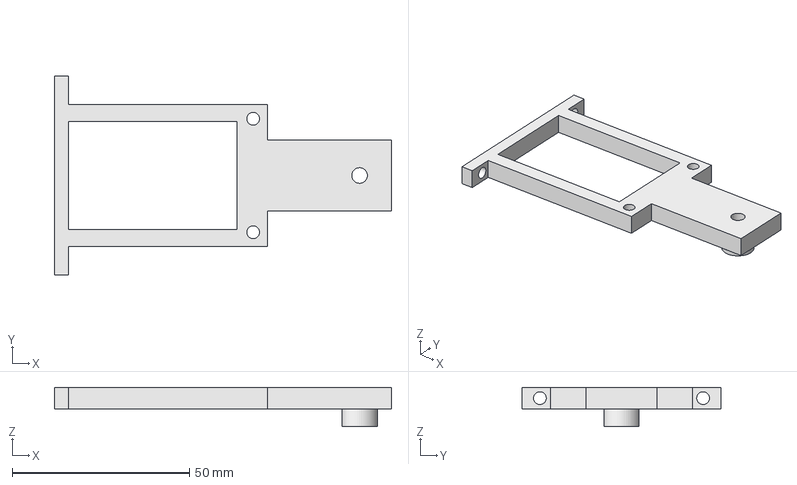
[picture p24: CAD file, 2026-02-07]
src/my_robot_description/mesh/CADv0.1/thighOuter.FCStd
95.0 x 56.0 x 11.0 mm

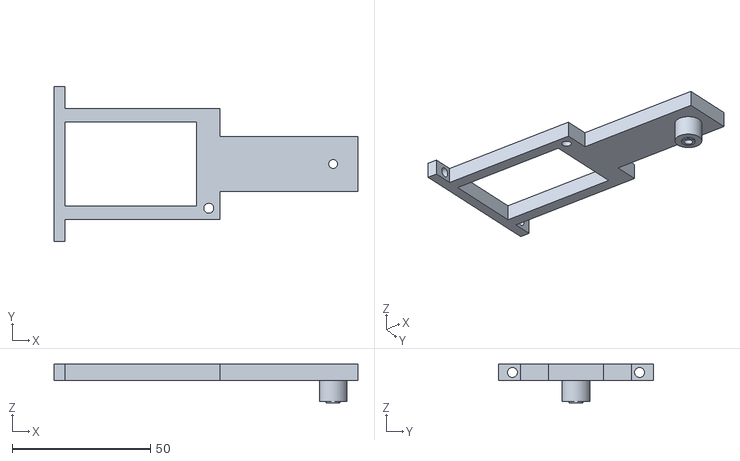
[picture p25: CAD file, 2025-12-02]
src/my_robot_description/mesh/CADv0/_mod_thighOuter-Body.stl
110.0 x 56.0 x 14.0

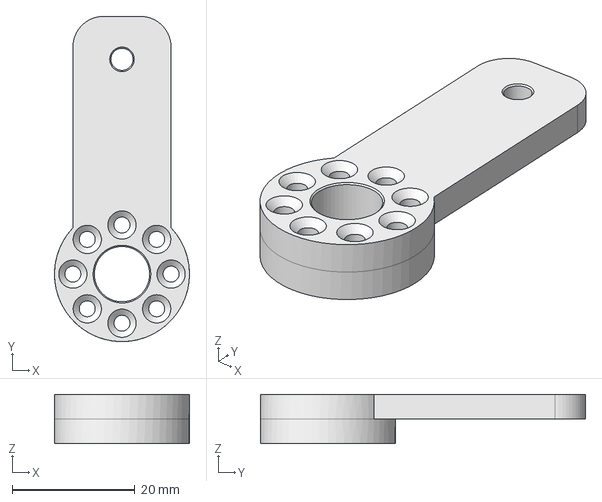
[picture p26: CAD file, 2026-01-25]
src/my_robot_description/mesh/CADv0.1/calfJoint.FCStd
22.0 x 53.0 x 8.00 mm

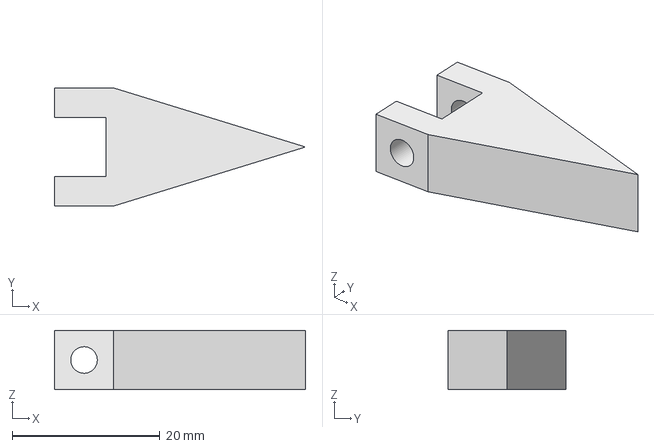
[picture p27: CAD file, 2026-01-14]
src/my_robot_description/mesh/CADv0.1/fanFlag.FCStd
34.0 x 16.0 x 8.00 mm

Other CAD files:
src/my_robot_description/mesh/CADv0.1/thighInner.FCStd
src/my_robot_description/mesh/CADv0/_mod_thighOuter_heatInsert.FCStd
src/my_robot_description/mesh/CADv0.1/basePlate.FCStd
src/my_robot_description/mesh/CADv0/_mod_thighOuter.FCStd
src/my_robot_description/mesh/CADv0.1/XL430holderBasic.FCStd
src/my_robot_description/mesh/CADv0.1/XL430holderBasic.stl
src/my_robot_description/mesh/CADv0.1/XL430holderThighBack.FCStd
src/my_robot_description/mesh/CADv0.1/XL430holderThighBack.stl
src/my_robot_description/mesh/CADv0.1/XL430holderThighFront.FCStd
src/my_robot_description/mesh/CADv0.1/XL430holderThighFront.stl
src/my_robot_description/mesh/CADv0.1/XL430rotorPadding.FCStd
src/my_robot_description/mesh/CADv0.1/XL430rotorPadding.stl
src/my_robot_description/mesh/CADv0.1/basePlate.stl
src/my_robot_description/mesh/CADv0.1/basePlateTorsoLower.stl
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

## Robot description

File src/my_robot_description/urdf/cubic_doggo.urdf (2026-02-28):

<?xml version="1.0" ?>
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
<robot name="cubic_doggo">
  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
  <ros2_control name="cubic_doggo_controller" type="system">
    <hardware>
      <plugin>mock_components/GenericSystem</plugin>
      <param name="servo1_channel_FR">11</param>
      <param name="servo2_channel_FR">12</param>
      <param name="servo3_channel_FR">13</param>
      <param name="servo1_channel_FL">11</param>
      <param name="servo2_channel_FL">12</param>
      <param name="servo3_channel_FL">13</param>
      <param name="servo1_channel_GR">11</param>
      <param name="servo2_channel_GR">12</param>
      <param name="servo3_channel_GR">13</param>
      <param name="servo1_channel_GL">11</param>
      <param name="servo2_channel_GL">12</param>
      <param name="servo3_channel_GL">13</param>
    </hardware>
    <joint name="servo1_servo1_padding_FR">
      <command_interface name="position"/>
      <state_interface name="position">
        <param name="initial_value">3.14</param>
      </state_interface>
      <state_interface name="velocity">
        <param name="initial_value">0.0</param>
      </state_interface>
      <state_interface name="effort">
        <param name="initial_value">0.0</param>
      </state_interface>
    </joint>
    <joint name="servo2_servo2_padding_FR">
      <command_interface name="position"/>
      <state_interface name="position">
        <param name="initial_value">3.14</param>
      </state_interface>
      <state_interface name="velocity">
        <param name="initial_value">0.0</param>
      </state_interface>
      <state_interface name="effort">
        <param name="initial_value">0.0</param>
      </state_interface>
    </joint>
    <joint name="servo3_calfFeet_FR">
      <command_interface name="position"/>
      <state_interface name="position">
        <param name="initial_value">3.14</param>
      </state_interface>
      <state_interface name="velocity">
        <param name="initial_value">0.0</param>
      </state_interface>
      <state_interface name="effort">
        <param name="initial_value">0.0</param>
      </state_interface>
    </joint>
    <joint name="servo1_servo1_padding_FL">
      <command_interface name="position"/>
      <state_interface name="position">
        <param name="initial_value">3.14</param>
      </state_interface>
      <state_interface name="velocity">
        <param name="initial_value">0.0</param>
      </state_interface>
      <state_interface name="effort">
        <param name="initial_value">0.0</param>
      </state_interface>
    </joint>
    <joint name="servo2_servo2_padding_FL">
      <command_interface name="position"/>
      <state_interface name="position">
        <param name="initial_value">3.14</param>
      </state_interface>
      <state_interface name="velocity">
        <param name="initial_value">0.0</param>
      </state_interface>
      <state_interface name="effort">
        <param name="initial_value">0.0</param>
      </state_interface>
    </joint>
    <joint name="servo3_calfFeet_FL">
      <command_interface name="position"/>
      <state_interface name="position">
        <param name="initial_value">3.14</param>
      </state_interface>
      <state_interface name="velocity">
        <param name="initial_value">0.0</param>
      </state_interface>
      <state_interface name="effort">
        <param name="initial_value">0.0</param>
      </state_interface>
    </joint>
    <joint name="servo1_servo1_padding_BR">
      <command_interface name="position"/>
      <state_interface name="position">
        <param name="initial_value">3.14</param>
      </state_interface>
      <state_interface name="velocity">
        <param name="initial_value">0.0</param>
      </state_interface>
      <state_interface name="effort">
        <param name="initial_value">0.0</param>
      </state_interface>
    </joint>
    <joint name="servo2_servo2_padding_BR">
      <command_interface name="position"/>
      <state_interface name="position">
        <param name="initial_value">3.14</param>
      </state_interface>
      <state_interface name="velocity">
        <param name="initial_value">0.0</param>
      </state_interface>
      <state_interface name="effort">
        <param name="initial_value">0.0</param>
      </state_interface>
    </joint>
    <joint name="servo3_calfFeet_BR">
      <command_interface name="position"/>
      <state_interface name="position">
        <param name="initial_value">3.14</param>
      </state_interface>
      <state_interface name="velocity">
        <param name="initial_value">0.0</param>
      </state_interface>
      <state_interface name="effort">
        <param name="initial_value">0.0</param>
      </state_interface>
    </joint>
    <joint name="servo1_servo1_padding_BL">
      <command_interface name="position"/>
      <state_interface name="position">
        <param name="initial_value">3.14</param>
      </state_interface>
      <state_interface name="velocity">
        <param name="initial_value">0.0</param>
      </state_interface>
      <state_interface name="effort">
        <param name="initial_value">0.0</param>
      </state_interface>
    </joint>
    <joint name="servo2_servo2_padding_BL">
      <command_interface name="position"/>
      <state_interface name="position">
        <param name="initial_value">3.14</param>
      </state_interface>
      <state_interface name="velocity">
        <param name="initial_value">0.0</param>
      </state_interface>
      <state_interface name="effort">
        <param name="initial_value">0.0</param>
      </state_interface>
    </joint>
    <joint name="servo3_calfFeet_BL">
      <command_interface name="position"/>
      <state_interface name="position">
        <param name="initial_value">3.14</param>
      </state_interface>
      <state_interface name="velocity">
        <param name="initial_value">0.0</param>
      </state_interface>
      <state_interface name="effort">
        <param name="initial_value">0.0</param>
      </state_interface>
    </joint>
  </ros2_control>
  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
  <link name="base_link">
    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
    <inertial>
      <mass value="0.0336"/>
      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
    </inertial>
  </link>
  <link name="base_plate_F">
    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
    <inertial>
      <mass value="0.0336"/>
      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
    </inertial>
  </link>
  <joint name="torso_base_plate_F" type="fixed">
    <parent link="base_link"/>
    <child link="base_plate_F"/>
    <origin rpy="0 0 0" xyz="0 -0.066 0.004"/>
  </joint>
  <link name="base_plate_B">
    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
    <inertial>
      <mass value="0.0336"/>
      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
    </inertial>
  </link>
  <joint name="torso_base_plate_B" type="fixed">
    <parent link="base_link"/>
    <child link="base_plate_B"/>
    <origin rpy="0 0 0" xyz="0 0.09 0.004"/>
  </joint>
  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
  <link name="servo1_holder_FL">
    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
    <inertial>
      <mass value="0.0098"/>
      <origin rpy="0 0 1.5707963" xyz="0 0 0.007"/>
      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
    </inertial>
  </link>
  <joint name="base_plate_servo1_holder_FL" type="fixed">
    <parent link="base_plate_F"/>
    <child link="servo1_holder_FL"/>
    <origin rpy="0 0 0" xyz="-0.052 0.018 0.004"/>
  </joint>
  <link name="servo1_FL">
    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
    <inertial>
      <mass value="0.0572"/>
      <origin rpy="1.5707963 0 0" xyz="0 0 0.02325"/>
      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
    </inertial>
  </link>
  <joint name="servo1_holder_servo1_FL" type="fixed">
    <parent link="servo1_holder_FL"/>
    <child link="servo1_FL"/>
    <origin rpy="0 0 0" xyz="0 0 0.008"/>
  </joint>
  <link name="servo1_padding_FL">
    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
    <inertial>
      <mass value="0.0013"/>
      <origin rpy="1.5707963 0 0" xyz="0 -0.002 0"/>
      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
    </inertial>
  </link>
  <joint name="servo1_servo1_padding_FL" type="revolute">
    <parent link="servo1_FL"/>
    <child link="servo1_padding_FL"/>
    <origin rpy="0 0 0" xyz="0 -0.019000000000000003 0.01125"/>
    <axis xyz="0 -1 0"/>
    <limit effort="1000.0" lower="2.0943950666666664" upper="4.188790133333334" velocity="20.0"/>
    <dynamics damping="0.1" friction="0.05"/>
  </joint>
  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

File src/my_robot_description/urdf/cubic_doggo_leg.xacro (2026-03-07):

<?xml version="1.0"?>
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
<robot xmlns:xacro="http://www.ros.org/wiki/xacro">
    <xacro:macro name="doggo_leg" params="prefix">

    <xacro:property name="servo_x" value="0.0285"/>
    <xacro:property name="servo_y" value="0.0465"/>
    <xacro:property name="servo_z" value="0.034"/>
    <xacro:if value="${prefix == 'FL'}">
        <xacro:property name="rflc" value=" 1"/>
        <xacro:property name="base_plate" value="base_plate_F"/>
        <xacro:property name="servo1_holder_xyz" value="-0.052 0.018 0.004"/>
    </xacro:if>
    <xacro:if value="${prefix == 'FR'}">
        <xacro:property name="rflc" value="-1"/>
        <xacro:property name="base_plate" value="base_plate_F"/>
        <xacro:property name="servo1_holder_xyz" value=" 0.052 0.018 0.004"/>
    </xacro:if>
    <xacro:if value="${prefix == 'BL'}">
        <xacro:property name="rflc" value=" 1"/>
        <xacro:property name="base_plate" value='base_plate_B'/>
        <xacro:property name="servo1_holder_xyz" value="-0.052 0.018 0.004"/>
    </xacro:if>
    <xacro:if value="${prefix == 'BR'}">
        <xacro:property name="rflc" value="-1"/>
        <xacro:property name="base_plate" value='base_plate_B'/>
        <xacro:property name="servo1_holder_xyz" value=" 0.052 0.018 0.004"/>
    </xacro:if> 

    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
    <link name="servo1_holder_${prefix}">
        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
        <xacro:box_inertia m="0.0098" x="0.037" y="0.037" z="0.014" o_xyz="0 0 0.007" o_rpy="0 0 ${urdf_pi/2}"/>
    </link> 
    <joint name="base_plate_servo1_holder_${prefix}" type="fixed">
        <parent link="${base_plate}"/>
        <child link="servo1_holder_${prefix}"/>
        <origin xyz="${servo1_holder_xyz}" rpy="0 0 0"/>
    </joint>
    
    <link name="servo1_${prefix}">
        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
        <xacro:box_inertia m="0.0572" x="${servo_x}" y="${servo_y}" z="${servo_z}" o_xyz="0 0 ${servo_y/2}" o_rpy="${urdf_pi/2} 0 0"/>
    </link> 
    <joint name="servo1_holder_servo1_${prefix}" type="fixed">
        <parent link="servo1_holder_${prefix}"/>
        <child link="servo1_${prefix}"/>
        <origin xyz="0 0 0.008" rpy="0 0 0"/>
    </joint>

    <link name="servo1_padding_${prefix}">
        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
        <xacro:cylinder_inertia m="0.0013" r="0.011" l="0.004" o_xyz="0 -0.002 0" o_rpy="${urdf_pi/2} 0 0"/>
    </link> 
    <joint name="servo1_servo1_padding_${prefix}" type="revolute">
        <parent link="servo1_${prefix}"/>
        <child link="servo1_padding_${prefix}"/>
        <origin xyz="0 ${-servo_z/2-0.002} ${0.01+0.0025/2}" rpy="0 0 0"/>
        <axis xyz="0 -1 0"/>
        <limit effort="1000.0" velocity="20.0" lower="${urdf_pi - urdf_pi/3}" upper="${urdf_pi + urdf_pi/3}"/>
        <dynamics friction="0.05" damping="0.1"/>
    </joint>

    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
    <link name="servo2_holder_${prefix}">
        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
        <xacro:box_inertia m="0.0098" x="0.037" y="0.037" z="0.014" o_xyz="0 -0.007 0" o_rpy="${urdf_pi/2} 0 0"/>
    </link> 
    <joint name="base_link_servo2_holder_${prefix}" type="fixed">
        <parent link="servo1_padding_${prefix}"/>
        <child link="servo2_holder_${prefix}"/>
        <origin xyz="0 -0.004 0" rpy="0 0 0"/>
    </joint>
    
    <link name="servo2_${prefix}">
        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
        <xacro:box_inertia m="0.0572" x="${servo_x}" y="${servo_y}" z="${servo_z}" o_xyz="0 ${-servo_y/2} 0" o_rpy="0 ${rflc*urdf_pi/2} 0"/>
    </link> 
    <joint name="servo2_holder_servo2_${prefix}" type="fixed">
        <parent link="servo2_holder_${prefix}"/>
        <child link="servo2_${prefix}"/>
        <origin xyz="0 -0.008 0" rpy="0 0 0"/>
    </joint>
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

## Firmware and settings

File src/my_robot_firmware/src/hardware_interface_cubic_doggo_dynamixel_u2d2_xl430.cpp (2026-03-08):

#include <iostream>
#include <chrono>
#include <thread>
#include "rclcpp/rclcpp.hpp"
#include "my_robot_firmware/hardware_interface_cubic_doggo_dynamixel_u2d2_xl430.hpp"

//////////////////////////////////////////////////////////////////////////////////////////////////////////////////////
namespace cubic_doggo_namespace {
    hardware_interface::CallbackReturn HardwareInterfaceU2D2_cubic_doggo::on_init
        (const hardware_interface::HardwareComponentInterfaceParams &params) 
    {
        if (hardware_interface::SystemInterface::on_init(params) !=
            hardware_interface::CallbackReturn::SUCCESS) {
            return hardware_interface::CallbackReturn::ERROR;
        }
        RCLCPP_INFO(get_logger(), "on_init()");

        dxl_return_ = dxl_wb_.init(PORT_NAME, BAUD_RATE, &log_);
        if (dxl_return_ == false) {
            RCLCPP_ERROR(get_logger(), "on_init(): failed to open the port %s!", PORT_NAME);
            return hardware_interface::CallbackReturn::ERROR;
        } else {
            RCLCPP_INFO(get_logger(), "on_init(): initialize with baud rate: %d", BAUD_RATE);
        } 


        /////////// see: src/my_robot_description/urdf/cubic_doggo.ros2_control.xacro
        servo_channels_[0]  = std::stoi(params.hardware_info.hardware_parameters.at("servo1_channel_FL"));
        servo_channels_[1]  = std::stoi(params.hardware_info.hardware_parameters.at("servo2_channel_FL"));
        servo_channels_[2]  = std::stoi(params.hardware_info.hardware_parameters.at("servo3_channel_FL"));
        servo_channels_[3]  = std::stoi(params.hardware_info.hardware_parameters.at("servo1_channel_FR"));
        servo_channels_[4]  = std::stoi(params.hardware_info.hardware_parameters.at("servo2_channel_FR"));
        servo_channels_[5]  = std::stoi(params.hardware_info.hardware_parameters.at("servo3_channel_FR"));
        servo_channels_[6]  = std::stoi(params.hardware_info.hardware_parameters.at("servo1_channel_BL"));
        servo_channels_[7]  = std::stoi(params.hardware_info.hardware_parameters.at("servo2_channel_BL"));
        servo_channels_[8]  = std::stoi(params.hardware_info.hardware_parameters.at("servo3_channel_BL"));
        servo_channels_[9]  = std::stoi(params.hardware_info.hardware_parameters.at("servo1_channel_BR"));
        servo_channels_[10] = std::stoi(params.hardware_info.hardware_parameters.at("servo2_channel_BR"));
        servo_channels_[11] = std::stoi(params.hardware_info.hardware_parameters.at("servo3_channel_BR"));
        joint_names = {"servo1_servo1_padding_FL", 
                       "servo2_servo2_padding_FL", 
                       "servo3_calfFeet_FL",
                       "servo1_servo1_padding_FR",
                       "servo2_servo2_padding_FR",
                       "servo3_calfFeet_FR",
                       "servo1_servo1_padding_BL",
                       "servo2_servo2_padding_BL",
                       "servo3_calfFeet_BL",
                       "servo1_servo1_padding_BR",
                       "servo2_servo2_padding_BR",
                       "servo3_calfFeet_BR"};
        rad_positions_init_[0]  = 3.04;                      
        rad_positions_init_[1]  = 2.54;                      //DXL_PI - DXL_PI/4.0;
        rad_positions_init_[2]  = 4.14;                      //DXL_PI - DXL_PI/8.0;
        rad_positions_init_[3]  = 3.24;                      
        rad_positions_init_[4]  = 3.74;                      //DXL_PI + DXL_PI/4.0;
        rad_positions_init_[5]  = 2.14;                      //DXL_PI + DXL_PI/8.0;
        rad_positions_init_[6]  = 3.04;                     
        rad_positions_init_[7]  = 2.54;                      //DXL_PI - DXL_PI/4.0;
        rad_positions_init_[8]  = 4.14;                      //DXL_PI - DXL_PI/8.0;
        rad_positions_init_[9]  = 3.24;                      
        rad_positions_init_[10] = 3.74;                      //DXL_PI + DXL_PI/4.0;
        rad_positions_init_[11] = 2.14;                      //DXL_PI + DXL_PI/8.0;
        ///////////
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

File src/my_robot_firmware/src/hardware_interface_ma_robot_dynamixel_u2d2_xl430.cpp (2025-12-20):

#include <iostream>
#include <chrono>
#include <thread>
#include "rclcpp/rclcpp.hpp"
#include "my_robot_firmware/hardware_interface_ma_robot_dynamixel_u2d2_xl430.hpp"

//////////////////////////////////////////////////////////////////////////////////////////////////////////////////////
namespace ma_robot_namespace {
    hardware_interface::CallbackReturn HardwareInterfaceU2D2_ma_robot::on_init
        (const hardware_interface::HardwareComponentInterfaceParams &params) 
    {
        if (hardware_interface::SystemInterface::on_init(params) !=
            hardware_interface::CallbackReturn::SUCCESS) {
            return hardware_interface::CallbackReturn::ERROR;
        }
        node_ = std::make_shared<rclcpp::Node>("HardwareInterfaceU2D2_ma_robot_node");
        RCLCPP_INFO(node_->get_logger(), "HardwareInterfaceU2D2_ma_robot::on_init()");
 
        dxl_return_ = dxl_wb_.init(PORT_NAME, BAUD_RATE, &log_);
        if (dxl_return_ == false) {
            RCLCPP_ERROR(node_->get_logger(), "Failed to open the port %s!", PORT_NAME);
            return hardware_interface::CallbackReturn::ERROR;
        } else {
            RCLCPP_INFO(node_->get_logger(), "Initialize with baud rate: %d", BAUD_RATE);
        } 

        joint1_servo_channel_ = std::stoi(params.hardware_info.hardware_parameters.at("joint1_servo_channel"));
        joint4_servo_channel_ = std::stoi(params.hardware_info.hardware_parameters.at("joint4_servo_channel"));
        joint6_servo_channel_ = std::stoi(params.hardware_info.hardware_parameters.at("joint6_servo_channel"));
        return hardware_interface::CallbackReturn::SUCCESS;     
    }
    hardware_interface::return_type HardwareInterfaceU2D2_ma_robot::read 
        (const rclcpp::Time & time, const rclcpp::Duration & period) 
    {
        //RCLCPP_INFO(node_->get_logger(), "HardwareInterfaceU2D2_ma_robot::read()");
        (void) time;
        (void) period;
        if (write_first_call_ == true) {
            start_time_ = time;
            write_first_call_ = false;
        }
        rclcpp::Duration lifetime = time - start_time_;
    
        // see: src/my_robot_description/urdf/ma_robot.ros2_control.xacro
        double joint1_position = channel_read_position_(joint1_servo_channel_); 
        double joint4_position = channel_read_position_(joint4_servo_channel_);
        double joint6_position = channel_read_position_(joint6_servo_channel_);
        set_state("joint1/position", joint1_position);
        set_state("joint2/position", joint2_position_);
        set_state("joint3/position", joint3_position_);
        set_state("joint4/position", joint4_position);
        set_state("joint5/position", joint5_position_);
        set_state("joint6/position", joint6_position);
        RCLCPP_INFO(node_->get_logger(), "read position (joint1, joint4, joint6): (%f, %f, %f)", 
                    joint1_position, joint4_position, joint6_position);
        return hardware_interface::return_type::OK;
    }
    hardware_interface::return_type HardwareInterfaceU2D2_ma_robot::write
        (const rclcpp::Time & time, const rclcpp::Duration & period) 
    {
        //RCLCPP_INFO(node_->get_logger(), "HardwareInterfaceU2D2_ma_robot::write()");
        (void) time;
        (void) period; 
        
        // see: src/my_robot_description/urdf/ma_robot.ros2_control.xacro
        double joint1_position = get_command("joint1/position");
        joint2_position_       = get_command("joint2/position");
        joint3_position_       = get_command("joint3/position");
        double joint4_position = get_command("joint4/position");
        joint5_position_       = get_command("joint5/position");
        double joint6_position = get_command("joint6/position");
        if (std::isnan(joint1_position) | std::isnan(joint2_position_) | std::isnan(joint3_position_) |
            std::isnan(joint4_position) | std::isnan(joint5_position_) | std::isnan(joint6_position)) {
            joint1_position  = 0.0;
            joint2_position_ = 0.0;
            joint3_position_ = 0.0;
            joint4_position  = 0.0;
            joint5_position_ = 0.0;
            joint6_position  = 0.0;
        }
        channel_set_position_(joint1_servo_channel_, joint1_position);
        channel_set_position_(joint4_servo_channel_, joint4_position);
        channel_set_position_(joint6_servo_channel_, joint6_position);
        RCLCPP_INFO(node_->get_logger(), "write position (joint1, joint4, joint6): (%f, %f, %f)",
                    joint1_position, joint4_position, joint6_position);
        return hardware_interface::return_type::OK;
    }
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

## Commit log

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2025-04-10 - initial attempt for running i2c with ros2 lifecycle - failed because cannot import board
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2025-10-07 - copying code from https://github.com/SphericalCowww/ROS_init_practice/tree/main/ros2_ws5_manipulator to test dynamixel with moveit
    [common_properties.xacro, joint_limits.yaml, ma_robot.gazebo.xacro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]
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2025-10-12 - did a comparison with udemy plugin code
    [ma_robot.ros2_control.xacro]
2025-10-12 - the servos do run at launch but has strange initial position and cannot receive commands
    [ma_robot.ros2_control.xacro]
2025-10-13 - resolve the radiant to dxl resolution convertion range/type issue. - set the servos only on joint1, joint4, and joint6 that have -pi to pi range
    [common_properties.xacro, ma_robot.ros2_control.xacro, ma_robot_arm.xacro]
2025-11-02 - adding the first peice of dynamixel bracket CAD
    [XL-430TTTT.FCStd]
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2025-11-04 - adding one more peice, 2 more to go
    [calfJoin.FCStd]
2025-11-05 - full one leg assembly. Quite some dimensional mismatch at the moment
    [calfFeet.FCStd, calfJoin.FCStd, calfLinkageRod.FCStd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]
2025-11-05 - one leg assembly so far. Will need to update the serevo holder dimentions
    [calfLinkageRod.FCStd, thighConn.FCStd, thighInner.FCStd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]
2025-11-06 - initial assembly of the full peices. Still some dimensional mismatch and some missing parts
    [XL-430TTTT.FCStd, basePlate.FCStd, calfJoin.FCStd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]
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2025-11-09 - adding the initial xacro file for the robot leg
    [XL-430TTTT-Body.stl, XL-430TTTT.FCStd, XL-430TTTT_mod-Body.stl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]
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2025-11-12 - more dimention update for 3d printing and bearing
    [_mod_XL-430TTTT.FCStd, _mod_calfJoint.FCStd, calfJoint.FCStd]
2025-11-15 - start extending dimensional adjustment outside the first two test peices
    [_mod_XL-430TTTT.FCStd, _mod_XL-430rotor.FCStd, _mod_calfJoint.FCStd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]
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2025-11-18 - modified _mod_thighConn into also a holder of a servo
    [_mod_XL-430TTTT.FCStd, _mod_thighConn.FCStd]
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2025-11-19 - screw holes attached to servo are too weak; broke with slight pressure from the bolt
    [_mod_XL-430TTTT.FCStd, _mod_basePlate.FCStd, _mod_thighConn.FCStd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]
2025-11-22 - quick dimension such as the transition rod connection is actually not from the middle of the bearing - added first 1leg assembly figure. To do for the dimensions: - side support for the thighs - th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
    [_mod_calfJoint.FCStd]
2025-11-23 - initial urdf for 1 leg, need actual rvis to determine the final positioning
    [XL-430holderBasic.FCStd, _mod_XL-430TTTT.FCStd, _mod_XL-430holderBasic.FCStd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]
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2025-11-23 - trying to launch initial urdf with vis
    [my_robot.urdf.xacro, my_robot_leg.xacro]
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2025-11-23 - experiencing not able to load mesh problem
    [my_robot_leg.xacro]
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2025-11-27 - adjust the dimension to take into account that if bolting too deep into the rotor, the rotor stucks - adding assembly with the correct orientation
    [_mod_calfJoint.FCStd, _mod_thighOuter.FCStd]
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2025-11-30 - resolving the mesh not loading problem
    [my_robot_leg.xacro]
2025-12-02 - quick CAD fix
    [zAssembly4Leg.FCStd]
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2025-12-03 - something went wrong with _mod_basePlate-Body.stl
    [_mod_basePlate-Body.stl]
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2025-12-04 - adding all the relevant peice in urdf, but much details still need update
    [common_properties.xacro, my_robot_leg.xacro]
2025-12-07 - the origin of the .stl part is important for the orientation in urdf - updating the moment of initial orientations in my_robot_leg.xacro
    [_mod_XL-430rotorPadding-Body.stl, _mod_XL-430rotorPadding.FCStd, _mod_calfJoint-Body.stl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]
2025-12-07 - initial completion of my_robot_leg.xacro, including all the collision geometry and moment of inertia checks
    [common_properties.xacro, my_robot.gazebo.xacro, my_robot_leg.xacro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]
2025-12-07 - correct the geometry, the feet was pointing at the opposite direction
    [my_robot_leg.xacro]
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2025-12-08 - lifting up the base main_board to avoid collision with ground + update collision geometry to sustain the T shape
    [my_robot_leg.xacro]
2025-12-08 - update the angle range to support initial angle of 0 degrees
    [my_robot_leg.xacro]
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2025-12-08 - couldn't set the endofactor to be the toe of the leg. Will redo moveit2 to try again
    [ros2_controllers.yaml]
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2025-12-14 - editing to allow moveit to control the tip of the feet "calfSphere" without using end effector. Instead use the chain instead of joint option in src/my_robot_moveit_config/config/my_robot.srdf
    [joint_limits.yaml, my_robot.ros2_control.xacro, my_robot_leg.xacro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]
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2025-12-20 - updated my_robot_commander.cpp; next to test the leg control with actual dynamixels - updated my_robot.gazebo.xacro; next to test the leg control with gazebo
    [my_robot.gazebo.xacro]
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2025-12-21 - following chatGPT's recommendation to remove my_robot.ros2_control.xacro and my_robot.urdf.xacro from /my_robot_moveit_config/config to avoid interference - leg safe servo test: testRaspPi5_dynamix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
    [my_robot.ros2_control.xacro, my_robot.urdf.xacro]
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2025-12-21 - fixing the initial conditions for hardware_interface_my_robot_dynamixel_u2d2_xl430.cpp; now fine to run on leg
    [hardware_interface_my_robot_dynamixel_u2d2_xl430.cpp]
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2025-12-25 - update to fortify XL-430holderBasic.FCStd - update to fully incorporated basePlate, basePlateConnector, batteryHolder, tested after trying to assemble the previous parts including controllers
    [XL-430holderBasic.FCStd, basePlate.FCStd, basePlateConnector.FCStd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]
2025-12-25 - problem syncing moveit and joint_state_broadcaster, gemini states: ros2 topic hz /joint_states If it is lower than 10Hz, MoveIt will often throw the "recent timestamp" error. You should aim for 30H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
    [my_robot_controllers.yaml, my_robot_leg.xacro, ros2_controllers.yaml]
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2025-12-26 - update the calfFeet.FCStd to make it thinner while having 2 beargins
    [calfFeet.FCStd]
2025-12-27 - updated basePlateConnector on the down-convertor location - adding the assemble main system with 1 leg
    [basePlate.FCStd, basePlateConnector.FCStd]
2025-12-27 - debugging the latency issue; hopefully resolved
    [my_robot_controllers.yaml]
2025-12-28 - finally resolve the problem of syncing moveit and joint_state via reentrant group
    [my_robot_controllers.yaml]
2025-12-31 - now my_robot.with_commander.launch.py loads actual moveit config, IK now available. - improving revolution limits for my_robot_leg.xacro
    [my_robot_leg.xacro]
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2026-01-02 - update initial walk gait with trajectory in my_robot_commander.cpp, but to be tested - update the weight of each 3D printed peice in my_robot_leg.xacro by physically measuring the weight of the pei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
    [my_robot_leg.xacro]
2026-01-03 - updating the torso length so that the legs won't collide
    [basePlateConnector.FCStd, basePlateTorsoLower.FCStd, basePlateTorsoUpper.FCStd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]
2026-01-03 - attempting to solve the Cartesian solution not found problem: found a moveit issue instead - used a different solver: kinematics_solver: kdl_kinematics_plugin/KDLKinematicsPlugin
    [kinematics.yaml]
2026-01-04 - CAD update: was told universal bearings don't need another bearing at attachment - initial pilz_industrial_motion_planner
    [calfFeet.FCStd, calfJoint.FCStd]
2026-01-06 - CAD update to remove the extra rotation bearing on the universal bearing - update the weight
    [calfFeet.FCStd, calfJoint.FCStd, my_robot_leg.xacro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]
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2026-01-10 - update the firmware such it also read out the velocity and effort (current) from dynamixel
    [my_robot.ros2_control.xacro, my_robot_leg.xacro, my_robot_leg_test.xacro]
2026-01-10 - still updating trying to solve the following error for pilz planning: [move_group.moveit.moveit.core.conversions]: Found empty JointState message
    [my_robot.gazebo.xacro, my_robot.urdf.xacro, my_robot_leg.xacro]
2026-01-11 - resolved the [move_group.moveit.moveit.core.conversions]: Found empty JointState message problem - pilz linear motion now available! Do remember to move to the starting post first though
    [joint_limits.yaml, my_robot_leg.xacro]
2026-01-14 - adding demo video for pilz - adding a quick flag CAD
    [fanFlag.FCStd]
2026-01-25 - making the upper/lower legs 70mm long and translation rod torque 35mm
    [calfFeet.FCStd, calfJoint.FCStd, thighOuter.FCStd]
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2026-01-27 - trying to debug TOTG - also ros2 param list seems to hang
    [my_robot_leg.xacro]
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2026-02-07 - editted the leg dimension again, just so the translation rod gives mimicking rotation for the feet joint
    [calfFeet.FCStd, thighOuter.FCStd]
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2026-02-16 - correct the mirror relection on rpy
    [cubic_doggo_leg.xacro]
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2026-02-20 - matching collision geometry with inertia
    [cubic_doggo_leg.xacro]
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2026-03-01 - correct some label mismatches
    [cubic_doggo.ros2_control.xacro]
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2026-03-03 - legNamedTarget_ not works, however the leg motion is done one by one...
2026-03-07 - adding an all_legs planning group for synchronous motion => to be tested
    [cubic_doggo_controllers.yaml, ros2_controllers.yaml]
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2026-03-21 - something went wrong for batteryHolder.FCStd, now fixed
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
